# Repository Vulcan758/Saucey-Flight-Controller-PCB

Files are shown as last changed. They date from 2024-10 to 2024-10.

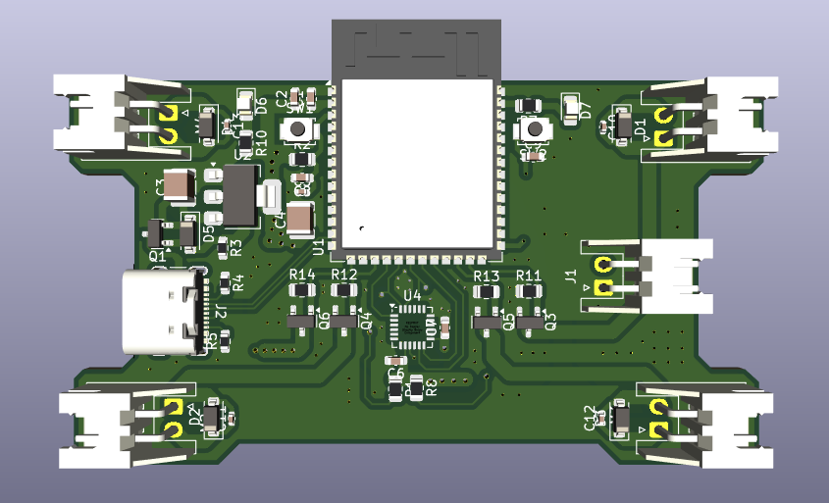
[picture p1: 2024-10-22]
images/Screenshot from 2024-10-21 20-56-30.png

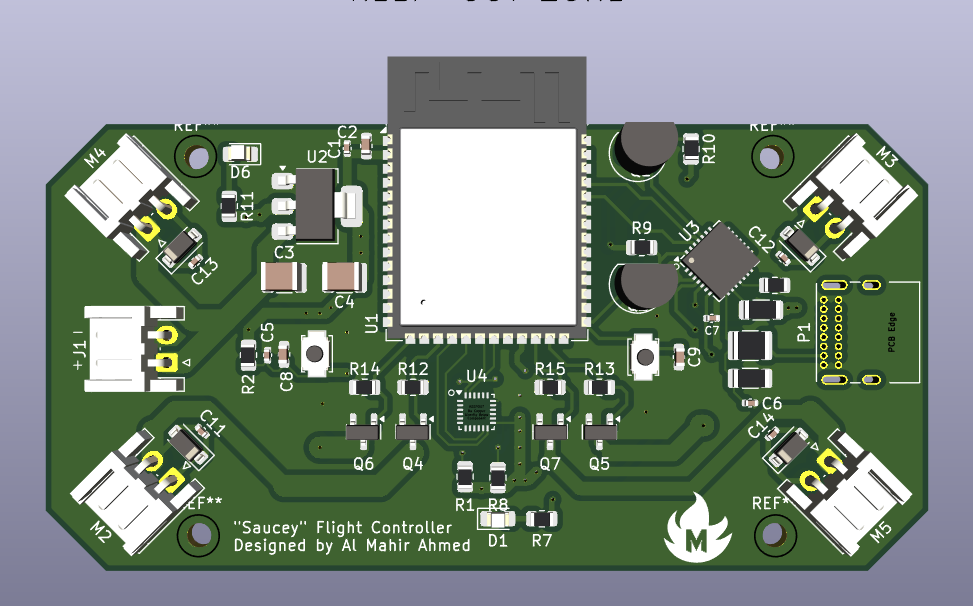
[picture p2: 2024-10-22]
v2/pics/Capture14.PNG

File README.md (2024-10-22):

# Saucey-Flight-Controller-PCB
This is a design repository for an ESP32 based flight controller (FC), "Saucey", that I made. 

Screenshot from 2024-10-21 20-56-30

## Technical Specifications
The FC uses an ESP32 S3 WROOM 1 module as the micrcontroller (MCU). It contains a 3.3 volt linear regulator (AMS1117 was used here) to power the MCU and the inertial measurement unit (IMU). The IMU used here is a MPU6050. This board is to be programmed through USB C. There is no onboard USB-Serial converter chip (such as CH2102) as ESP32 S3 can be programmed directly with its built USB-Serial converter on pins 18 and 19. A status LED is also availiable on board for testing and debugging. The FC board has 4 half bridge SI2306 logic level MOSFETs meant to drive coreless motors via JST connectors. This can however drive/ignite model rocket motors, LEDs and other low voltage output devices.

The goal of this project was to design a smart flight controller board with a credit card size form factor.

## PCB Schematic

Screenshot from 2024-10-22 01-19-56

## PCB Layout

Screenshot from 2024-10-22 01-10-28

### Top Layer

With ground pour

Screenshot from 2024-10-22 01-11-43

Without ground pour

Screenshot from 2024-10-22 01-11-12

### Bottom Layer

With ground pour

Screenshot from 2024-10-22 01-11-51

Without ground pour

Screenshot from 2024-10-22 01-11-23

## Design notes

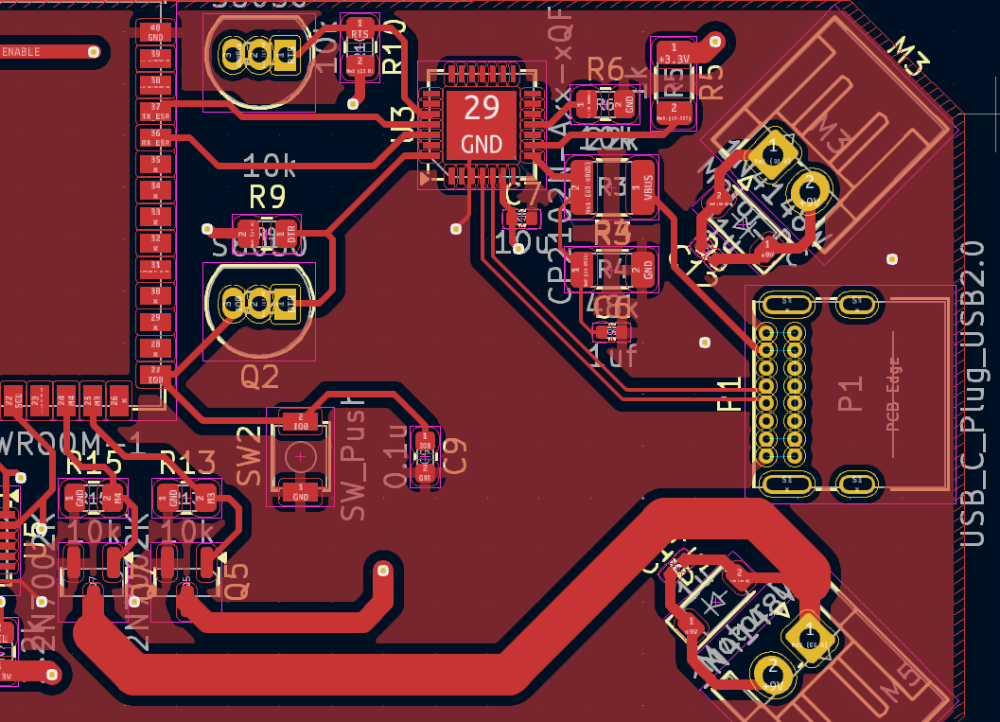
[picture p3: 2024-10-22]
v2/pics/Capture2.PNG

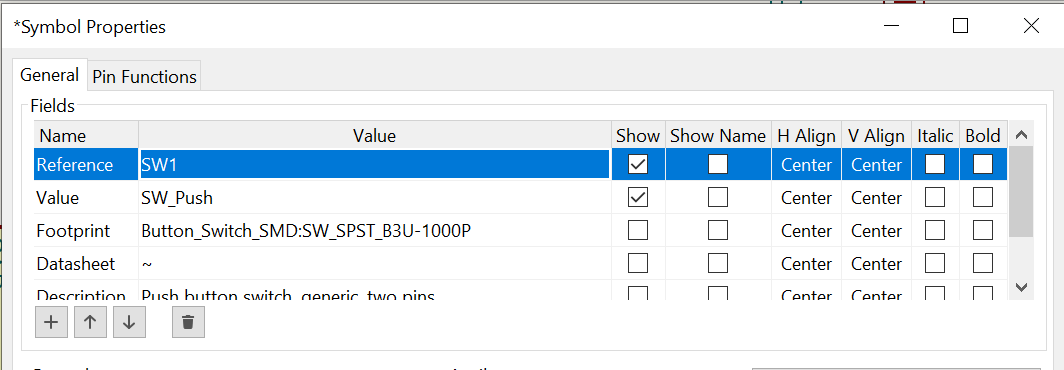
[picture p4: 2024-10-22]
v2/pics/SW_1_footprint.PNG

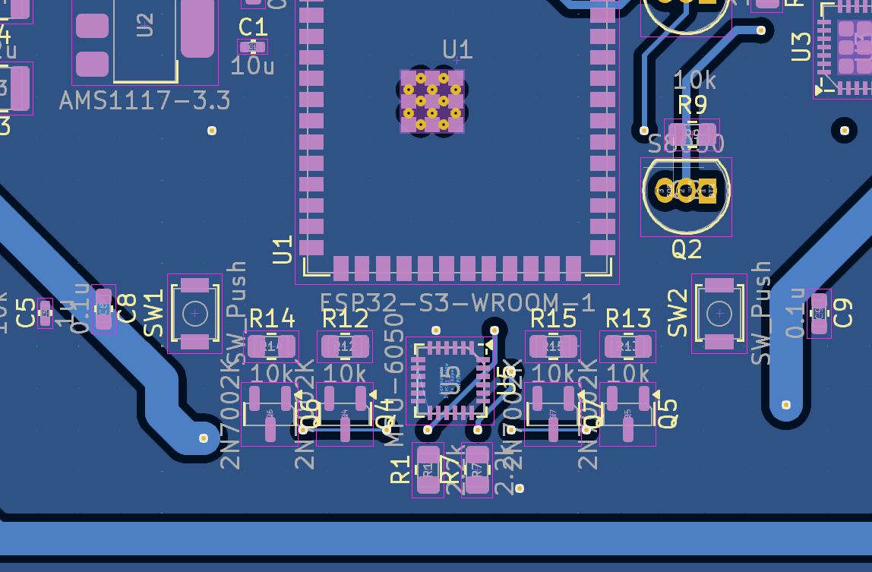
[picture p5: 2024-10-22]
v2/pics/Capture6.PNG

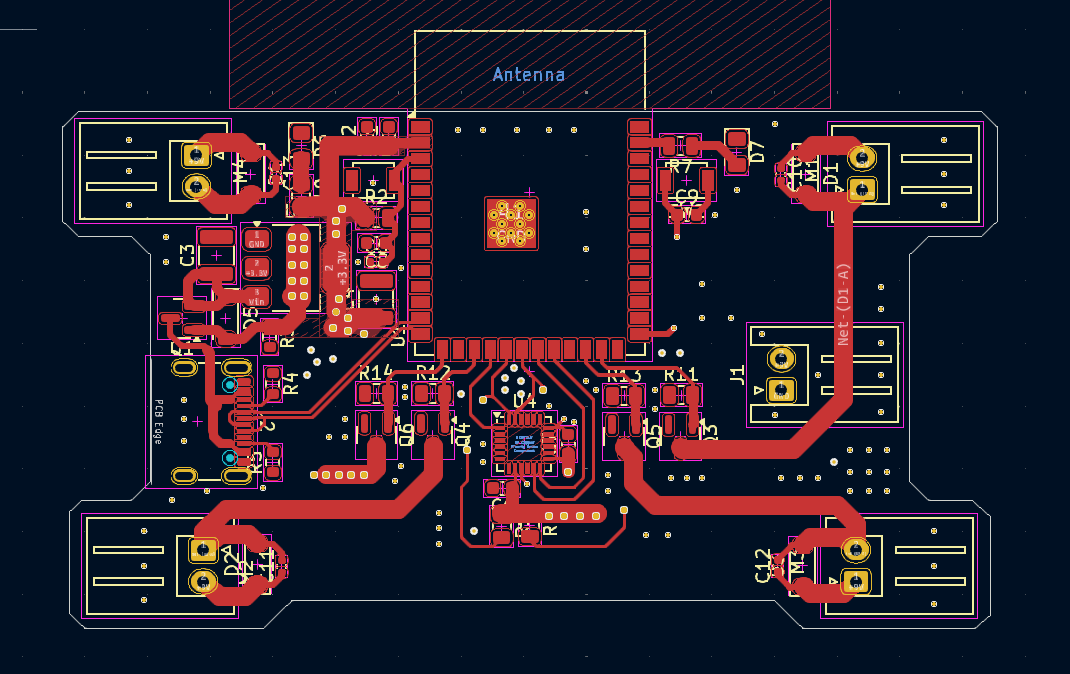
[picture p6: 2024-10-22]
images/Screenshot from 2024-10-22 01-11-12.png

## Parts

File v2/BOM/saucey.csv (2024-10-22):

Comment | Designator | Footprint
0.1u | C2,C8,C9 | Capacitor_SMD:C_0603_1608Metric
1u | C5,C11,C12,C13,C14 | Capacitor_SMD:C_0402_1005Metric
1uf | C6 | Capacitor_SMD:C_0402_1005Metric
10u | C1,C7 | Capacitor_SMD:C_0603_1608Metric
22u | C3,C4 | Capacitor_SMD:C_1210_3225Metric
1k | R5 | Resistor_SMD:R_1206_3216Metric
2.2k | R1,R8 | Resistor_SMD:R_0805_2012Metric
10k | R2,R6,R7,R9,R10,R11,R12,R13,R14,R15 | Resistor_SMD:R_0805_2012Metric
22k | R3 | Resistor_SMD:R_1210_3225Metric
48k | R4 | Resistor_SMD:R_1206_3216Metric
1N4148W | D2,D3,D4,D5 | Diode_SMD:D_SOD-123
AMS1117-3.3 | U2 | Package_TO_SOT_SMD:SOT-223-3_TabPin2
Conn_01x02_Socket | J1 | Connector_JST:JST_XH_S2B-XH-A_1x02_P2.50mm_Horizontal
CP2102N-A02-GQFN28 | U3 | Package_DFN_QFN:QFN-28-1EP_5x5mm_P0.5mm_EP3.35x3.35mm
ESP32-S3-WROOM-1 | U1 | RF_Module:ESP32-S3-WROOM-1
LED | D1,D6 | LED_SMD:LED_0805_2012Metric_Pad1.15x1.40mm_HandSolder
Motor JST | M5 | Connector_JST:JST_XH_S2B-XH-A_1x02_P2.50mm_Horizontal
Motor_DC | M2,M3,M4 | Connector_JST:JST_XH_S2B-XH-A_1x02_P2.50mm_Horizontal
MPU-6050 | U4 | Sensor_Motion:InvenSense_QFN-24_4x4mm_P0.5mm
S8050 | Q1,Q2 | Package_TO_SOT_THT:TO-92_Inline
SI2306 | Q4,Q5,Q6,Q7 | Package_TO_SOT_SMD:SOT-23
SW_Push | SW1,SW2 | Button_Switch_SMD:SW_SPST_B3U-1000P
USB_C_Plug_USB2.0 | P1 | Connector_USB:USB_C_Receptacle_GCT_USB4105-xx-A_16P_TopMnt_Horizontal

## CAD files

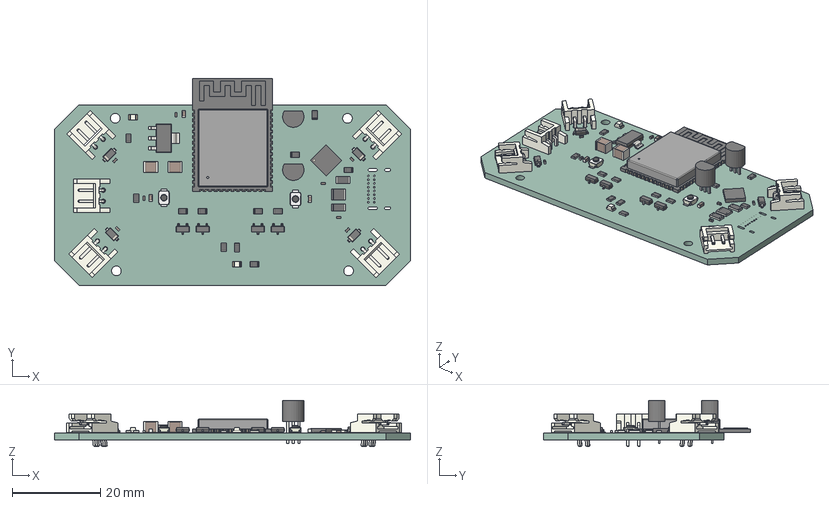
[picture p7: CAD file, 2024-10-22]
v2/step/saucey.step
80.5 x 46.7 x 10.5 mm
C_1210_3225Metric x 2
SOT_23 x 4
R_0805_2012Metric x 12
JST_S2B_EH x 5
SW_SPST_B3U-1000P x 2
TO-92_Inline_Narrow x 2
ESP32-S3-WROOM-1
C_0603_1608Metric x 3
D_SOD_123 x 4
LED_0805_2012Metric x 2
R_1206_3216Metric x 2
R_1210_3225Metric
C_0402_1005Metric x 8
QFN-28-1EP_5x5mm_Pitch0.5mm
SOT_223
saucey_PCB

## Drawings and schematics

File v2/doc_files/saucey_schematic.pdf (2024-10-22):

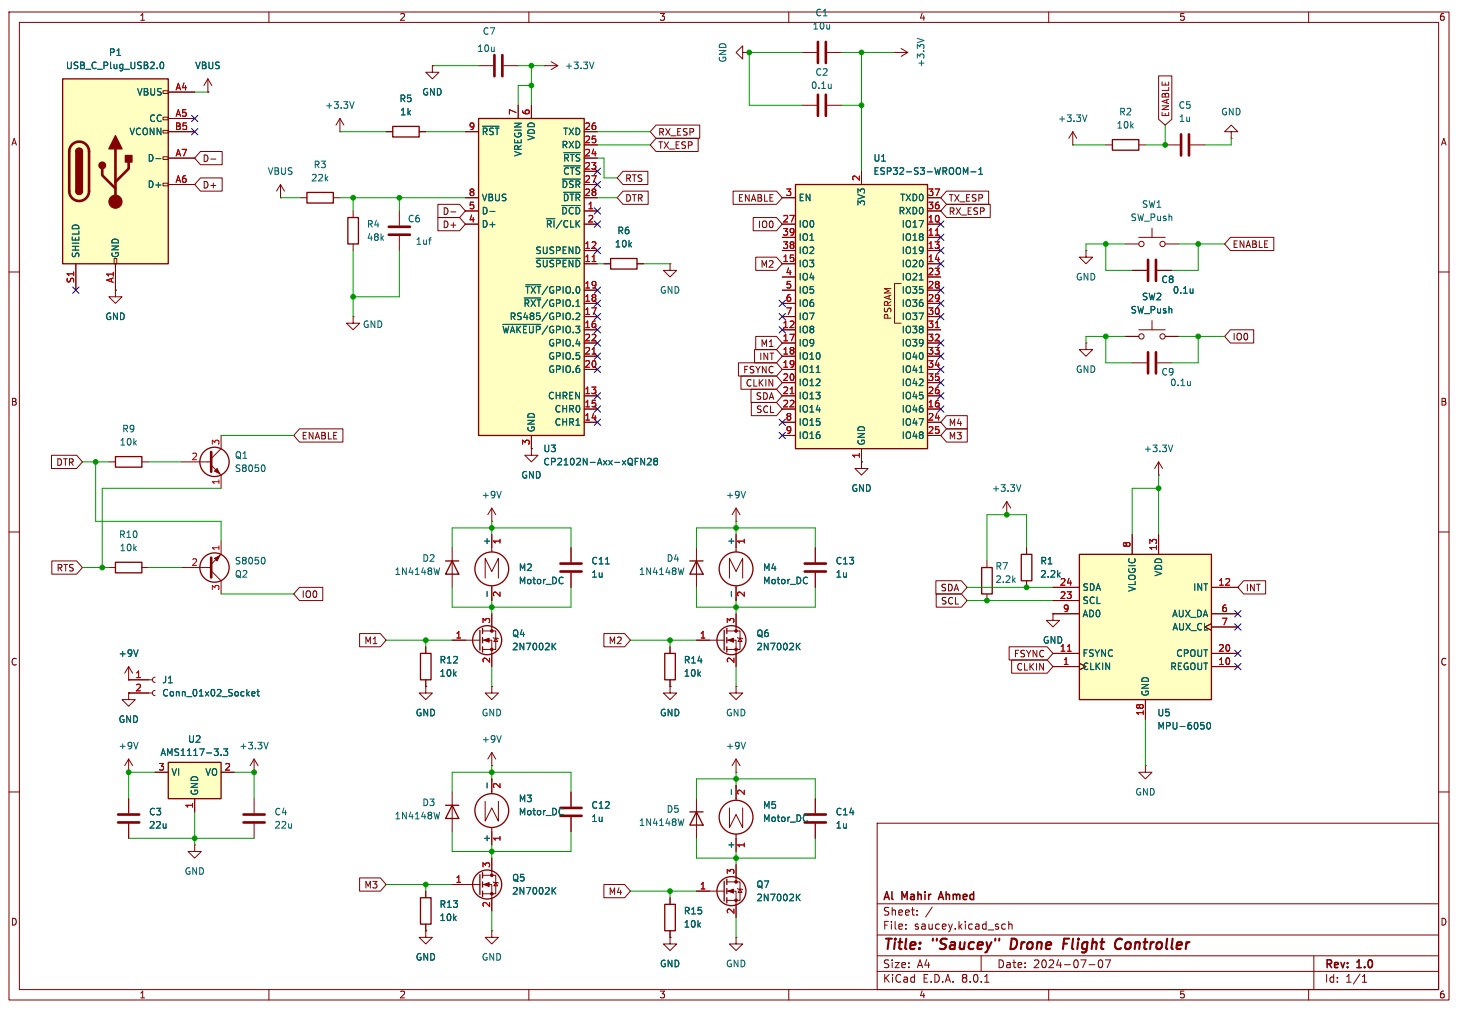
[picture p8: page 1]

-2 M3 Motor_DC +3.3V GND A1 VBUS A4 CC A5 D+ A6 D- A7 VCONN B5 SHIELD S1 P1 USB_C_Plug_USB2.0 PSRAM GND

7 VBUS 8 ~{RST} 9 P1 USB_C_Plug_USB2.0 GND A1 VBUS A4 CC A5 D+ A6 D- A7 VCONN B5 SHIELD S1 VBUS GND GND M3 Motor_DC

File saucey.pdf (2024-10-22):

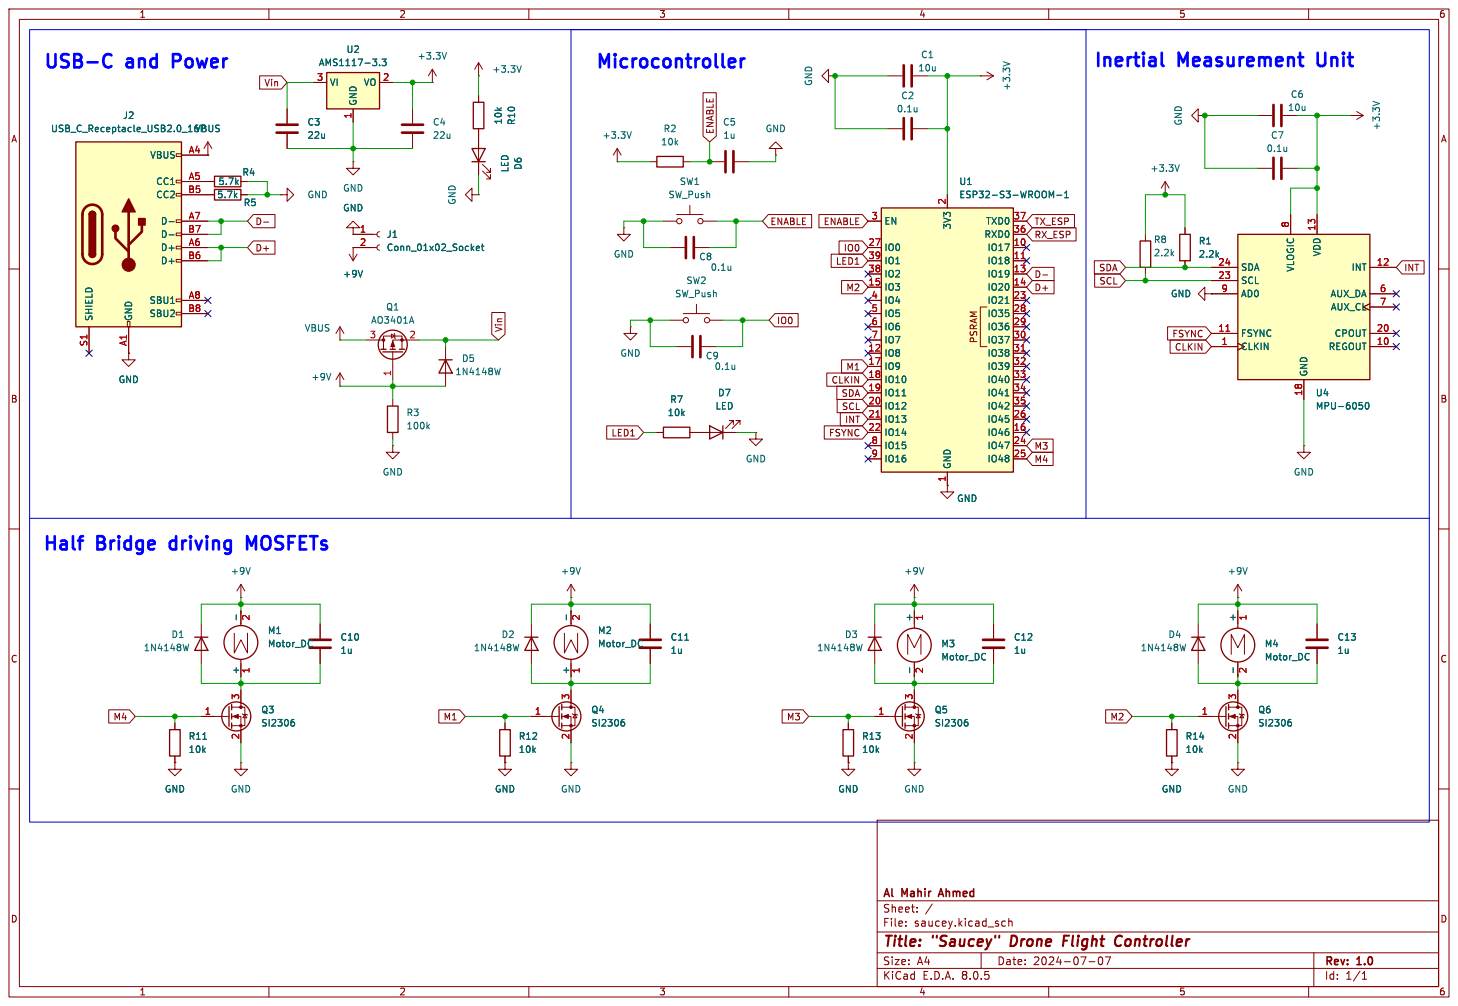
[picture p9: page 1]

Half Bridge driving MOSFETs

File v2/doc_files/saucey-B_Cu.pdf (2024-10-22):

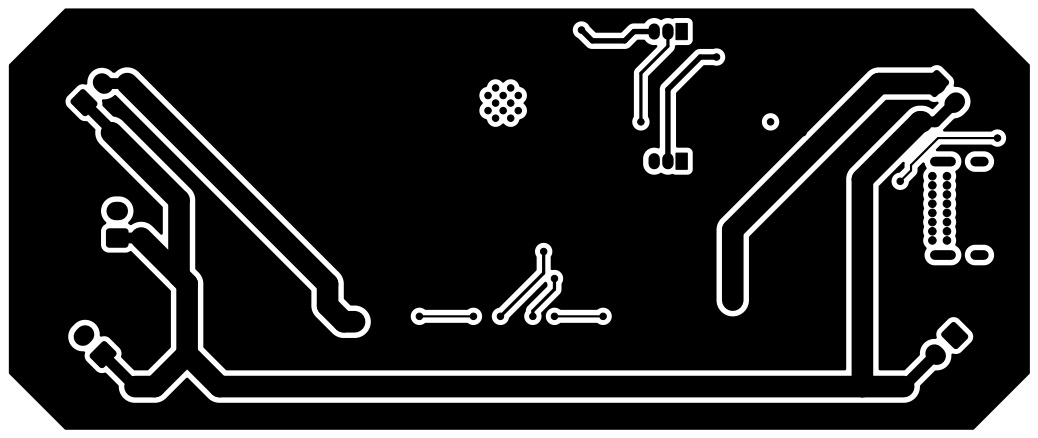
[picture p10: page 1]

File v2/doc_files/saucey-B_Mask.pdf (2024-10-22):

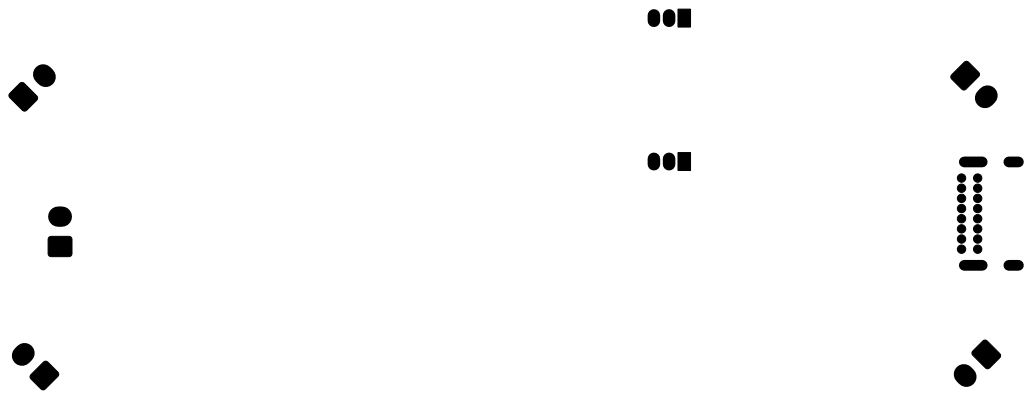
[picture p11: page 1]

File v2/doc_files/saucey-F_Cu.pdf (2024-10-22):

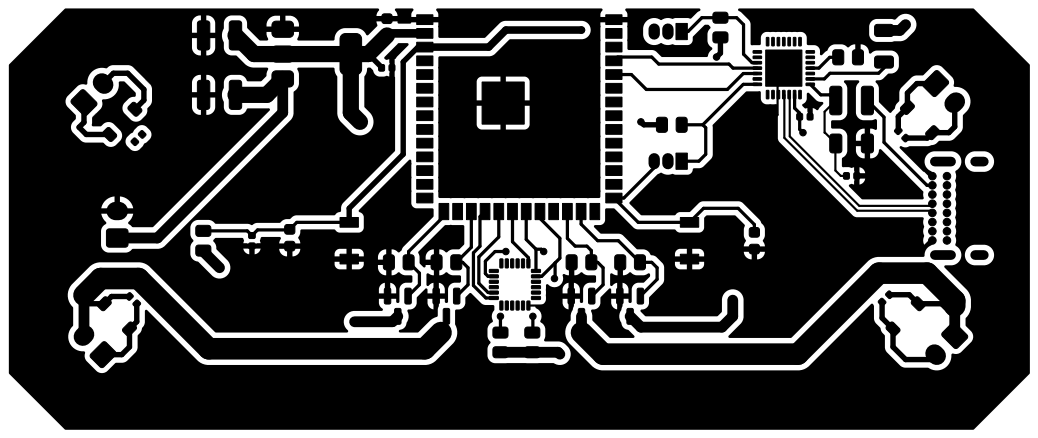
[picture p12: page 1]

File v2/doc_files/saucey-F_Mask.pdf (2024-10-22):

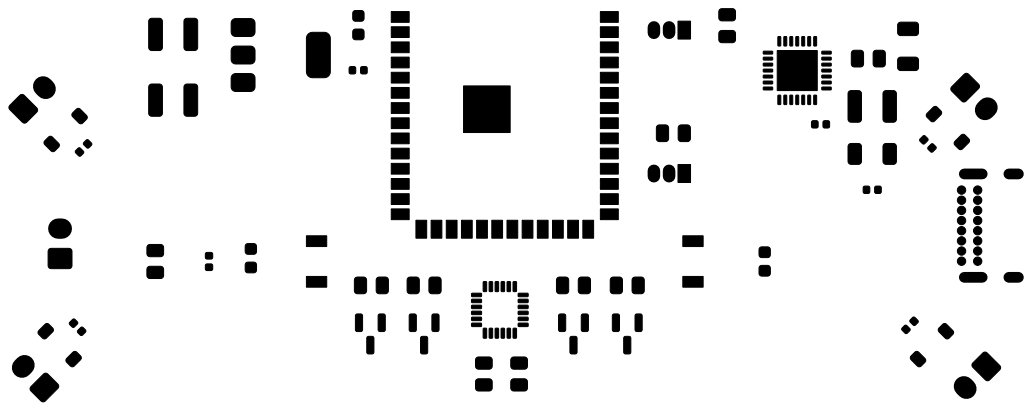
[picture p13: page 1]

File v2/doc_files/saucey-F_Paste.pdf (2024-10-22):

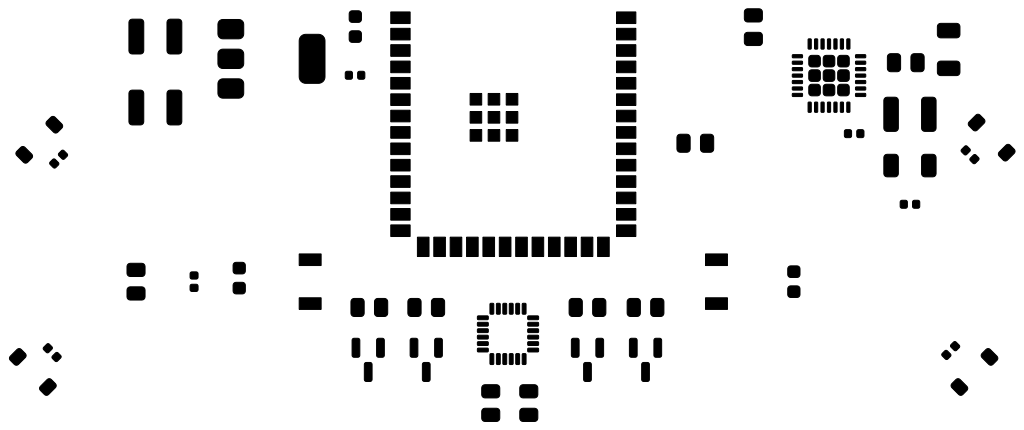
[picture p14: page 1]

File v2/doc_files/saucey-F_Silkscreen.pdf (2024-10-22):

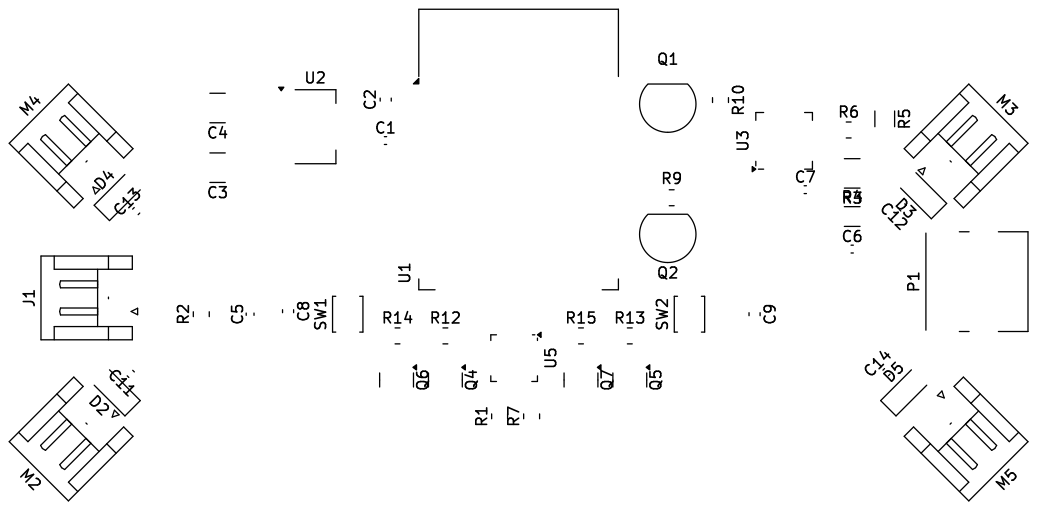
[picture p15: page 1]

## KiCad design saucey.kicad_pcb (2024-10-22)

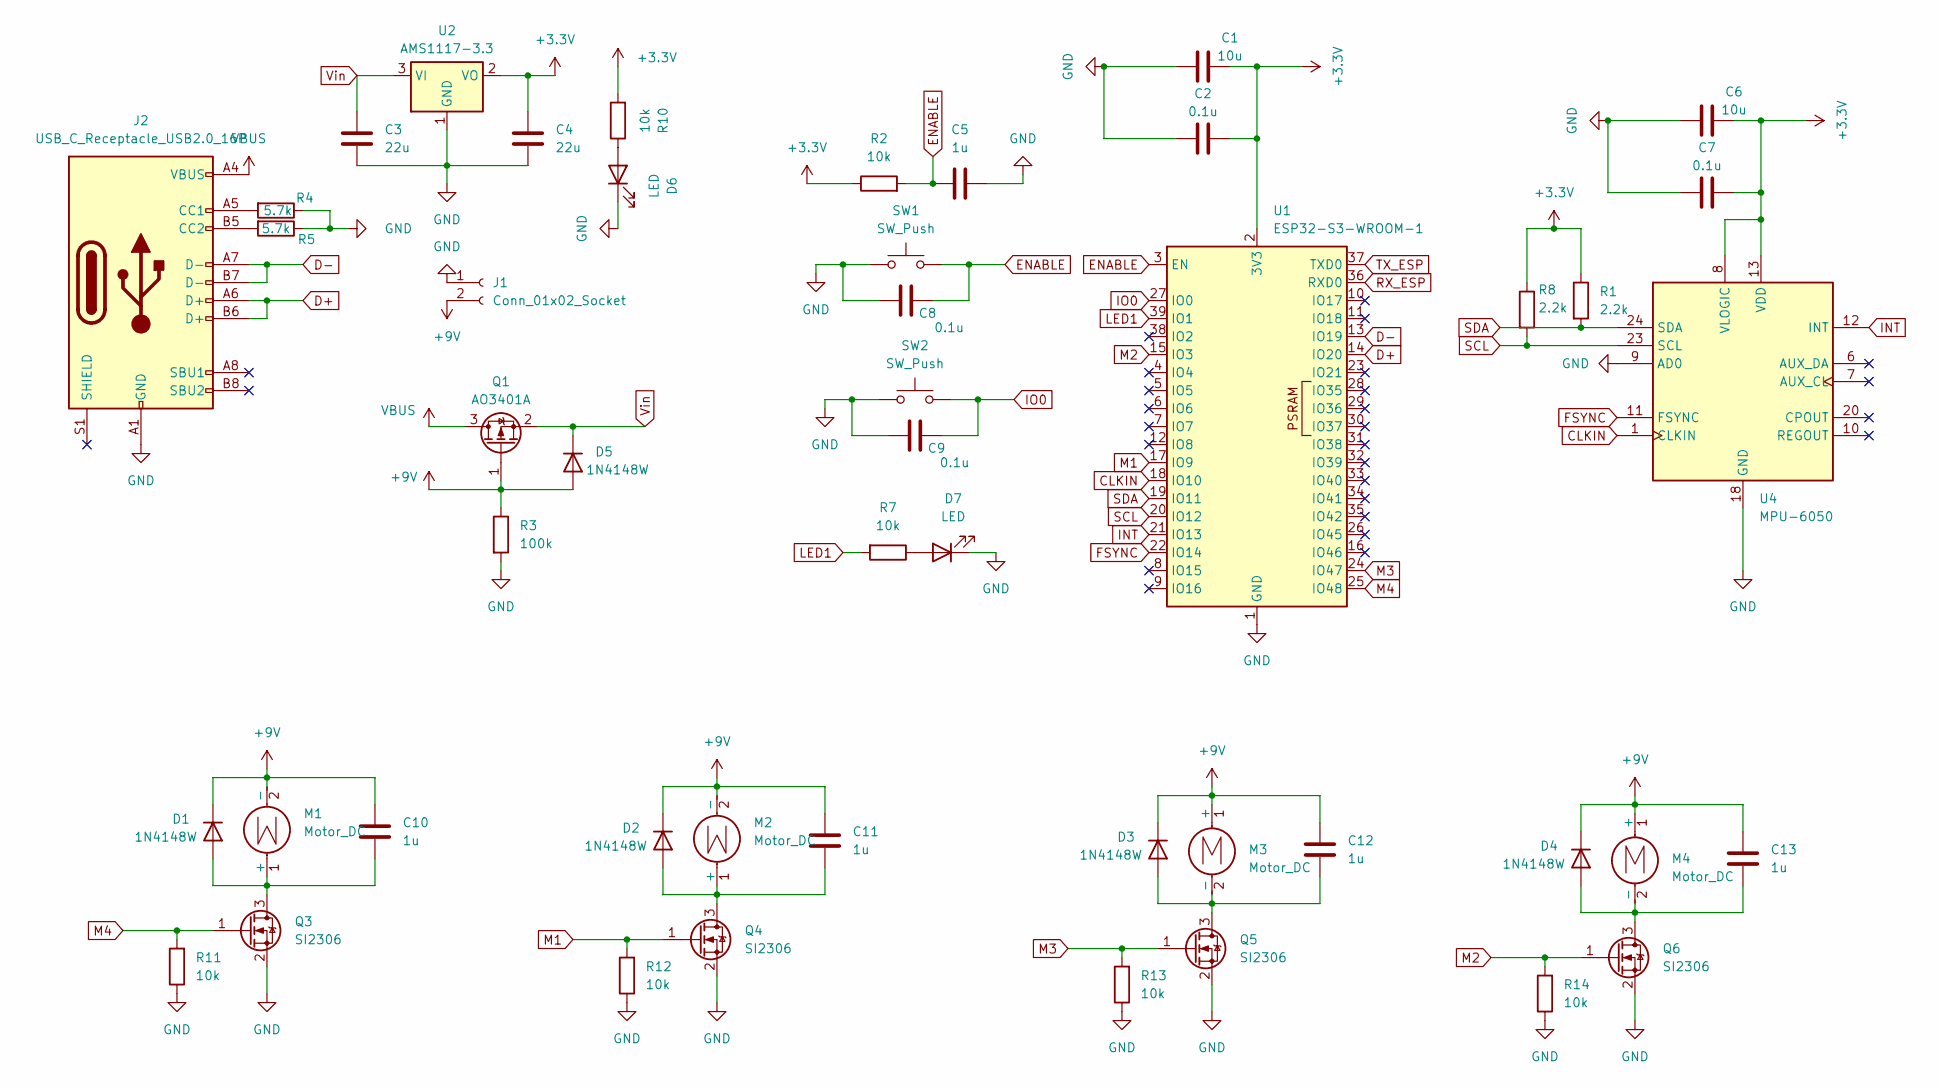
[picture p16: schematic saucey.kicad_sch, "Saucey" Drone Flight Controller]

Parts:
C1, C6: 10u; C_0603_1608Metric
C2, C7, C8, C9: 0.1u; C_0603_1608Metric
C3, C4: 22u; C_1210_3225Metric
C5, C10, C11, C12, C13: 1u; C_0402_1005Metric
D1, D2, D3, D4, D5: 1N4148W; D_SOD-123
D6, D7: LED; LED_0805_2012Metric_Pad1.15x1.40mm_HandSolder
J1: Conn_01x02_Socket; JST_XH_S2B-XH-A_1x02_P2.50mm_Horizontal
J2: USB_C_Receptacle_USB2.0_16P; USB_C_Receptacle_GCT_USB4105-xx-A_16P_TopMnt_Horizontal
M1, M2, M3, M4: Motor_DC; JST_XH_S2B-XH-A_1x02_P2.50mm_Horizontal
Q1: AO3401A; SOT-23
Q3, Q4, Q5, Q6: SI2306; SOT-23
R1, R8: 2.2k; R_0805_2012Metric
R2, R7, R10, R11, R12, R13, R14: 10k; R_0805_2012Metric
R3: 100k; R_0603_1608Metric
R4, R5: 5.7k; R_0603_1608Metric
SW1, SW2: SW_Push; SW_SPST_B3U-1000P
U1: ESP32-S3-WROOM-1
U2: AMS1117-3.3; SOT-223-3_TabPin2
U4: MPU-6050; InvenSense_QFN-24_4x4mm_P0.5mm

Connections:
+3.3V: C1.1, C2.1, C4.1, C6.1, C7.1, R1.1, R2.1, R8.1, R10.2, U1.2 (3V3), U2.2 (VO), U4.8 (VLOGIC), U4.13 (VDD)
+9V: C10.1, C11.1, C12.1, C13.1, D1.1 (K), D2.1 (K), D3.1 (K), D4.1 (K), D5.2 (A), J1.2, M1.2 (-), M2.2 (-), M3.1 (+), M4.1 (+), Q1.1 (G), R3.1
CLKIN: U1.18 (IO10), U4.1 (CLKIN)
D+: J2.A6 (D+), J2.B6 (D+), U1.14 (IO20)
D-: J2.A7 (D-), J2.B7 (D-), U1.13 (IO19)
ENABLE: C5.2, C8.1, R2.2, SW1.2, U1.3 (EN)
FSYNC: U1.22 (IO14), U4.11 (FSYNC)
GND: C1.2, C2.2, C3.2, C4.2, C5.1, C6.2, C7.2, C8.2, C9.2, D6.1 (K), D7.1 (K), J1.1, J2.A1 (GND), J2.A12 (GND), J2.B1 (GND), J2.B12 (GND), Q3.2 (S), Q4.2 (S), Q5.2 (S), Q6.2 (S), R3.2, R4.1, R5.1, R11.1, R12.1, R13.1, R14.1, SW1.1, SW2.1, U1.1 (GND), U1.40 (GND), U1.41 (GND), U2.1 (GND), U4.9 (AD0), U4.18 (GND)
INT: U1.21 (IO13), U4.12 (INT)
IO0: C9.1, SW2.2, U1.27 (IO0)
LED1: R7.2, U1.39 (IO1)
M1: Q4.1 (G), R12.2, U1.17 (IO9)
M2: Q6.1 (G), R14.2, U1.15 (IO3)
M3: Q5.1 (G), R13.2, U1.24 (IO47)
M4: Q3.1 (G), R11.2, U1.25 (IO48)
unnamed: C10.2, D1.2 (A), M1.1 (+), Q3.3 (D)
unnamed: C11.2, D2.2 (A), M2.1 (+), Q4.3 (D)
unnamed: C12.2, D3.2 (A), M3.2 (-), Q5.3 (D)
unnamed: C13.2, D4.2 (A), M4.2 (-), Q6.3 (D)
unnamed: D6.2 (A), R10.1
unnamed: D7.2 (A), R7.1
unnamed: J2.A5 (CC1), R4.2
unnamed: J2.B5 (CC2), R5.2
RX_ESP: U1.36 (RXD0)
SCL: R8.2, U1.20 (IO12), U4.23 (SCL)
SDA: R1.2, U1.19 (IO11), U4.24 (SDA)
TX_ESP: U1.37 (TXD0)
VBUS: J2.A4 (VBUS), J2.A9 (VBUS), J2.B4 (VBUS), J2.B9 (VBUS), Q1.3 (D)
Vin: C3.1, D5.1 (K), Q1.2 (S), U2.3 (VI)

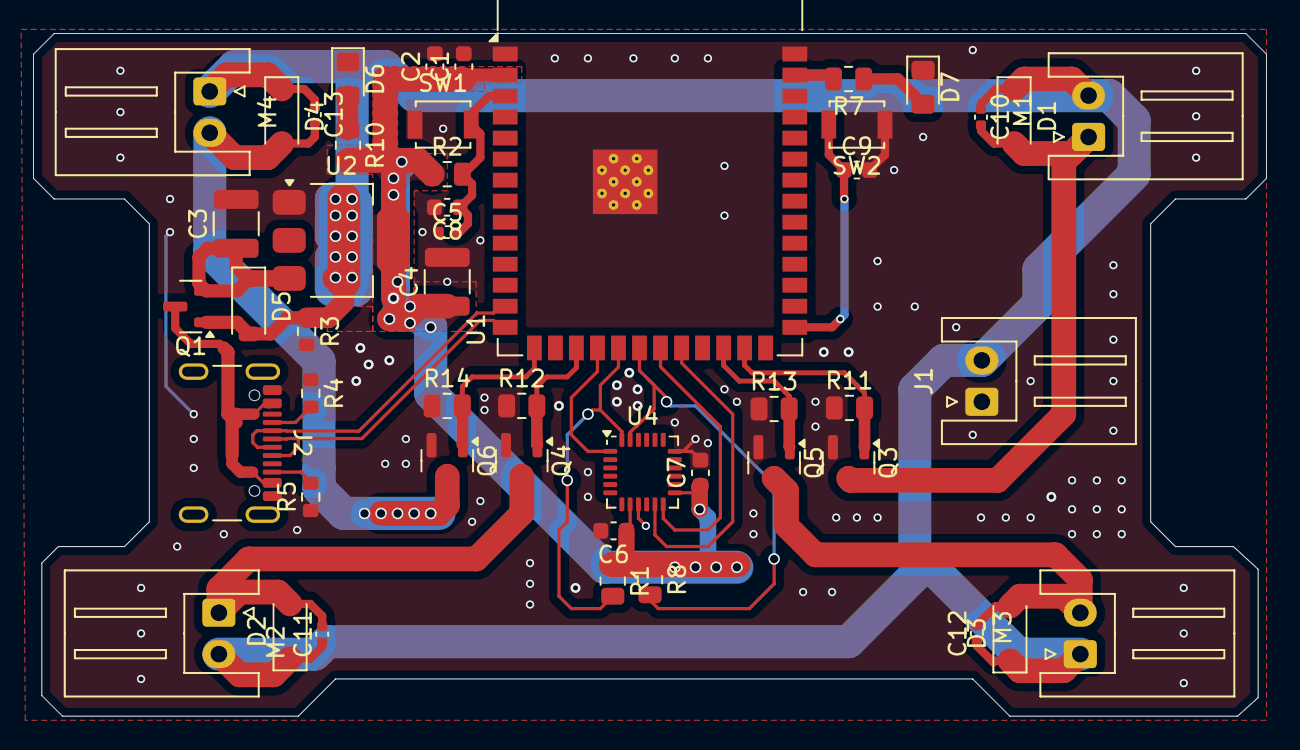
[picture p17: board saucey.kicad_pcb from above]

Board: 2 copper layers, 74.5 x 41.2 mm, 48 parts (0 on the bottom side), 27 nets.

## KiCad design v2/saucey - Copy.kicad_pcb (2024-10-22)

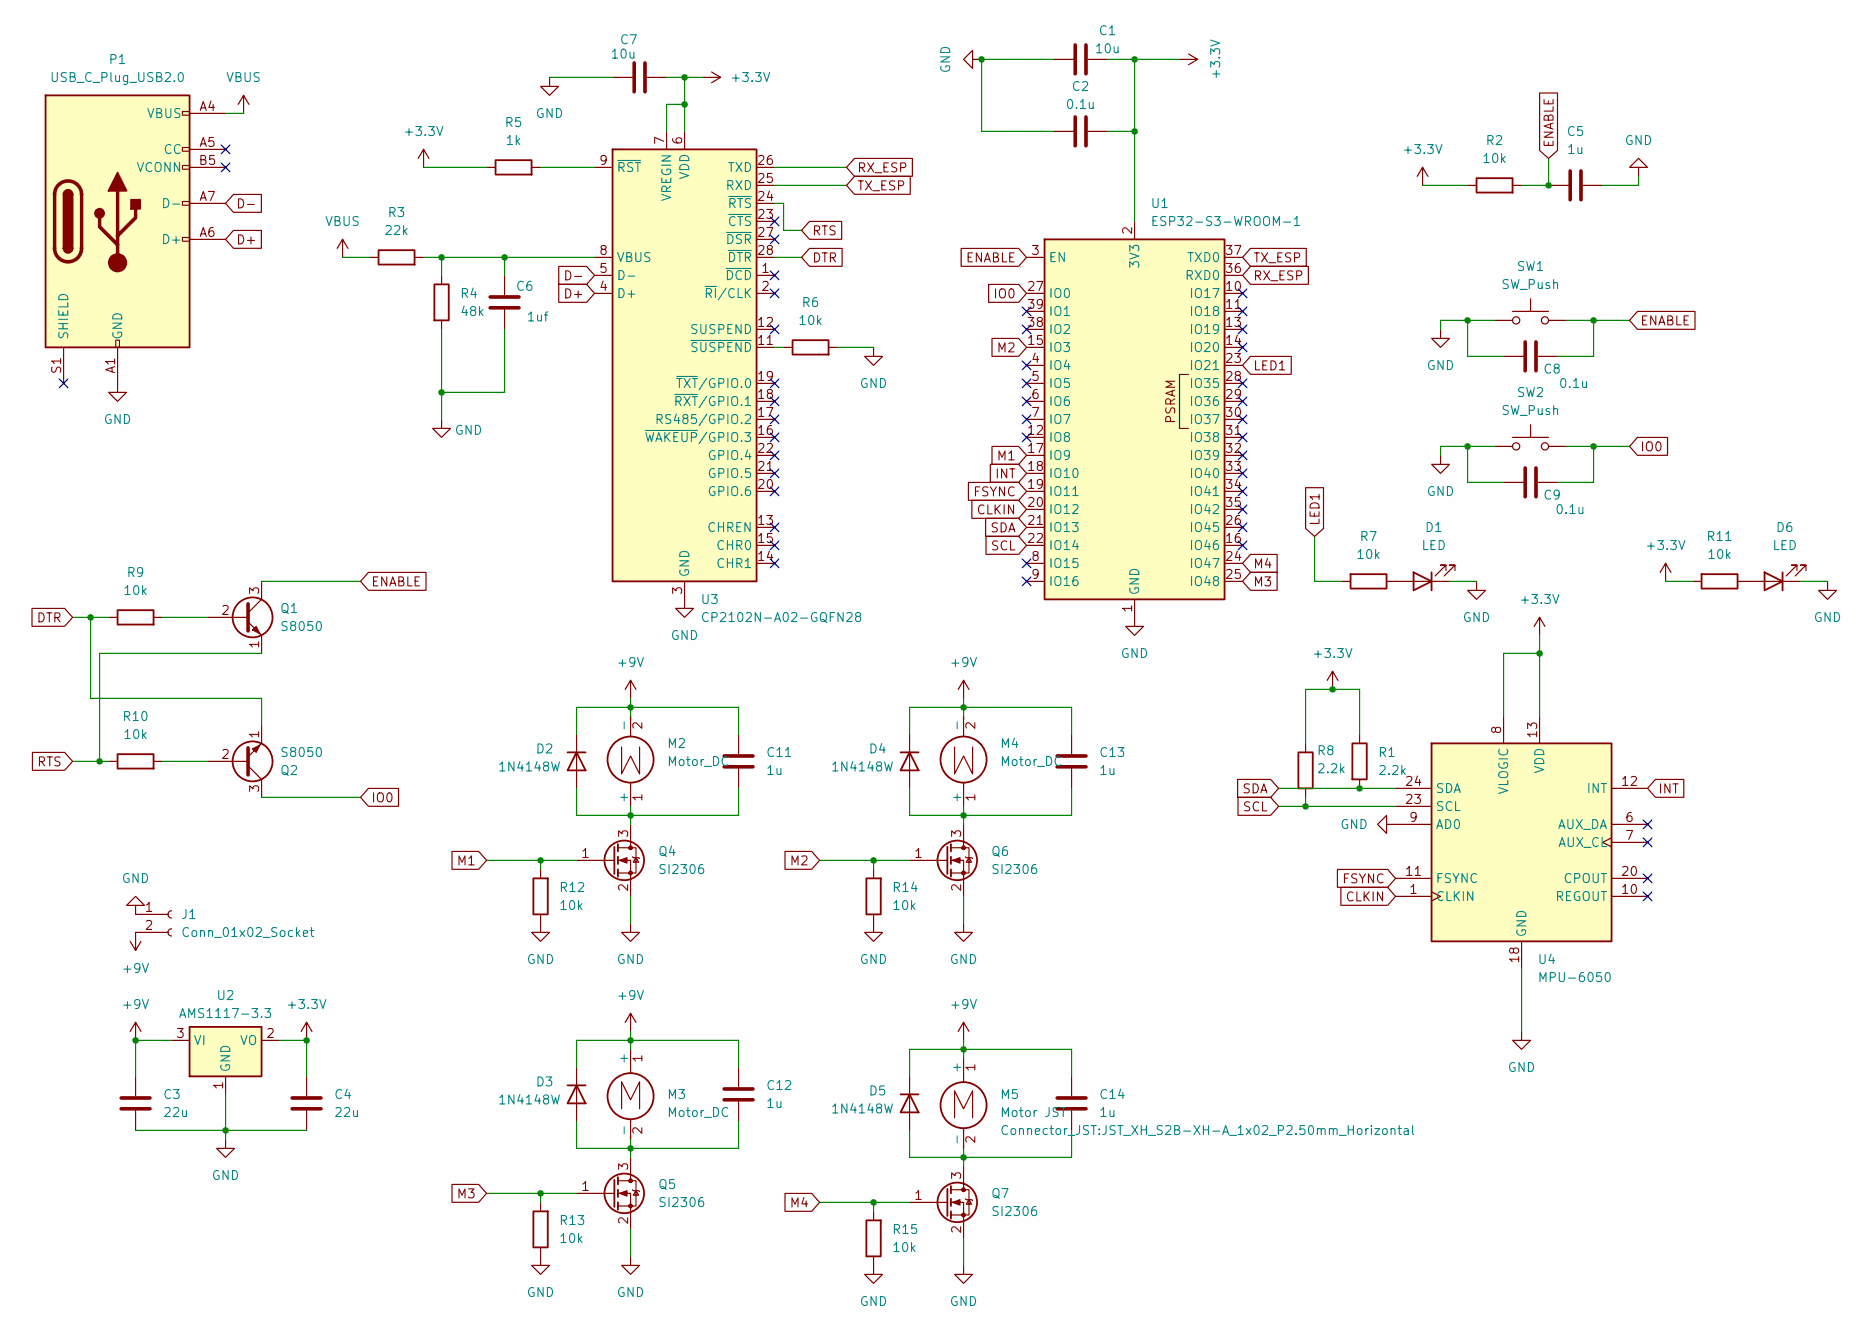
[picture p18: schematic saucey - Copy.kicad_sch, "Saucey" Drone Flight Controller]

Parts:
C1, C7: 10u; C_0603_1608Metric
C2, C8, C9: 0.1u; C_0603_1608Metric
C3, C4: 22u; C_1210_3225Metric
C5, C11, C12, C13, C14: 1u; C_0402_1005Metric
C6: 1uf; C_0402_1005Metric
D1, D6: LED; LED_0805_2012Metric_Pad1.15x1.40mm_HandSolder
D2, D3, D4, D5: 1N4148W; D_SOD-123
J1: Conn_01x02_Socket; JST_XH_S2B-XH-A_1x02_P2.50mm_Horizontal
M2, M3, M4: Motor_DC; JST_XH_S2B-XH-A_1x02_P2.50mm_Horizontal
M5: Motor JST; JST_XH_S2B-XH-A_1x02_P2.50mm_Horizontal
P1: USB_C_Plug_USB2.0; USB_C_Receptacle_GCT_USB4105-xx-A_16P_TopMnt_Horizontal
Q1, Q2: S8050; TO-92_Inline
Q4, Q5, Q6, Q7: SI2306; SOT-23
R1, R8: 2.2k; R_0805_2012Metric
R2, R6, R7, R9, R10, R11, R12, R13, R14, R15: 10k; R_0805_2012Metric
R3: 22k; R_1210_3225Metric
R4: 48k; R_1206_3216Metric
R5: 1k; R_1206_3216Metric
SW1, SW2: SW_Push; SW_SPST_B3U-1000P
U1: ESP32-S3-WROOM-1
U2: AMS1117-3.3; SOT-223-3_TabPin2
U3: CP2102N-A02-GQFN28; QFN-28-1EP_5x5mm_P0.5mm_EP3.35x3.35mm
U4: MPU-6050; InvenSense_QFN-24_4x4mm_P0.5mm

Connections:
+3.3V: C1.1, C2.1, C4.1, C7.1, R1.1, R2.1, R5.1, R8.1, R11.2, U1.2 (3V3), U2.2 (VO), U3.6 (VDD), U3.7 (VREGIN), U4.8 (VLOGIC), U4.13 (VDD)
+9V: C3.1, C11.1, C12.1, C13.1, C14.1, D2.1 (K), D3.1 (K), D4.1 (K), D5.1 (K), J1.2, M2.2 (-), M3.1 (+), M4.2 (-), M5.1 (+), U2.3 (VI)
CLKIN: U1.20 (IO12), U4.1 (CLKIN)
D+: P1.A6 (D+), U3.4 (D+)
D-: P1.A7 (D-), U3.5 (D-)
DTR: Q2.1 (E), R9.1, U3.28 (~DTR)
ENABLE: C5.2, C8.1, Q1.3 (C), R2.2, SW1.2, U1.3 (EN)
FSYNC: U1.19 (IO11), U4.11 (FSYNC)
GND: C1.2, C2.2, C3.2, C4.2, C5.1, C6.2, C7.2, C8.2, C9.2, D1.1 (K), D6.1 (K), J1.1, P1.A1 (GND), P1.A12 (GND), P1.B1 (GND), P1.B12 (GND), Q4.2 (S), Q5.2 (S), Q6.2 (S), Q7.2 (S), R4.2, R6.2, R12.1, R13.1, R14.1, R15.1, SW1.1, SW2.1, U1.1 (GND), U1.40 (GND), U1.41 (GND), U2.1 (GND), U3.3 (GND), U3.29 (GND), U4.9 (AD0), U4.18 (GND)
INT: U1.18 (IO10), U4.12 (INT)
IO0: C9.1, Q2.3 (C), SW2.2, U1.27 (IO0)
LED1: R7.2, U1.23 (IO21)
M1: Q4.1 (G), R12.2, U1.17 (IO9)
M2: Q6.1 (G), R14.2, U1.15 (IO3)
M3: Q5.1 (G), R13.2, U1.25 (IO48)
M4: Q7.1 (G), R15.2, U1.24 (IO47)
unnamed: D1.2 (A), R7.1
unnamed: C11.2, D2.2 (A), M2.1 (+), Q4.3 (D)
unnamed: C12.2, D3.2 (A), M3.2 (-), Q5.3 (D)
unnamed: C13.2, D4.2 (A), M4.1 (+), Q6.3 (D)
unnamed: C14.2, D5.2 (A), M5.2 (-), Q7.3 (D)
unnamed: D6.2 (A), R11.1
unnamed: Q1.2 (B), R9.2
unnamed: Q2.2 (B), R10.2
unnamed: C6.1, R3.2, R4.1, U3.8 (VBUS)
unnamed: R5.2, U3.9 (~RST)
unnamed: R6.1, U3.11 (~SUSPEND)
RTS: Q1.1 (E), R10.1, U3.24 (~RTS)
RX_ESP: U1.36 (RXD0), U3.26 (TXD)
SCL: R8.2, U1.22 (IO14), U4.23 (SCL)
SDA: R1.2, U1.21 (IO13), U4.24 (SDA)
TX_ESP: U1.37 (TXD0), U3.25 (RXD)
VBUS: P1.A4 (VBUS), P1.A9 (VBUS), P1.B4 (VBUS), P1.B9 (VBUS), R3.1

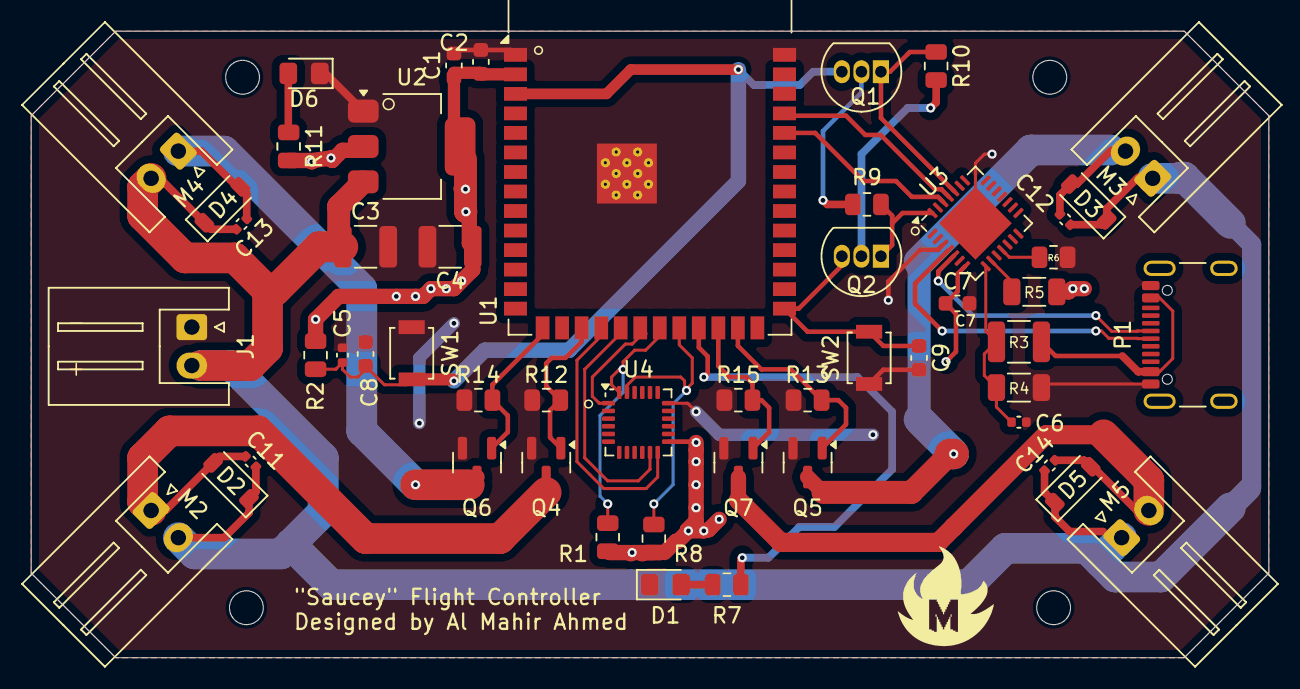
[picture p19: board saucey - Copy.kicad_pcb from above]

Board: 2 copper layers, 80.5 x 40.8 mm, 52 parts (0 on the bottom side), 33 nets.
